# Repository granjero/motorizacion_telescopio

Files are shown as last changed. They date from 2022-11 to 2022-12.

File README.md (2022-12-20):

# 🔭 Montura Dobson Motorizada

https://github.com/granjero/telescopio

Proyecto para motorizar/robotizar la montura Dobson del telescopio modelo que se realiza en el curso de fabricación de telescopios de la ASARAMAS (https://amigosdelaastronomia.org/)  
&nbsp;  
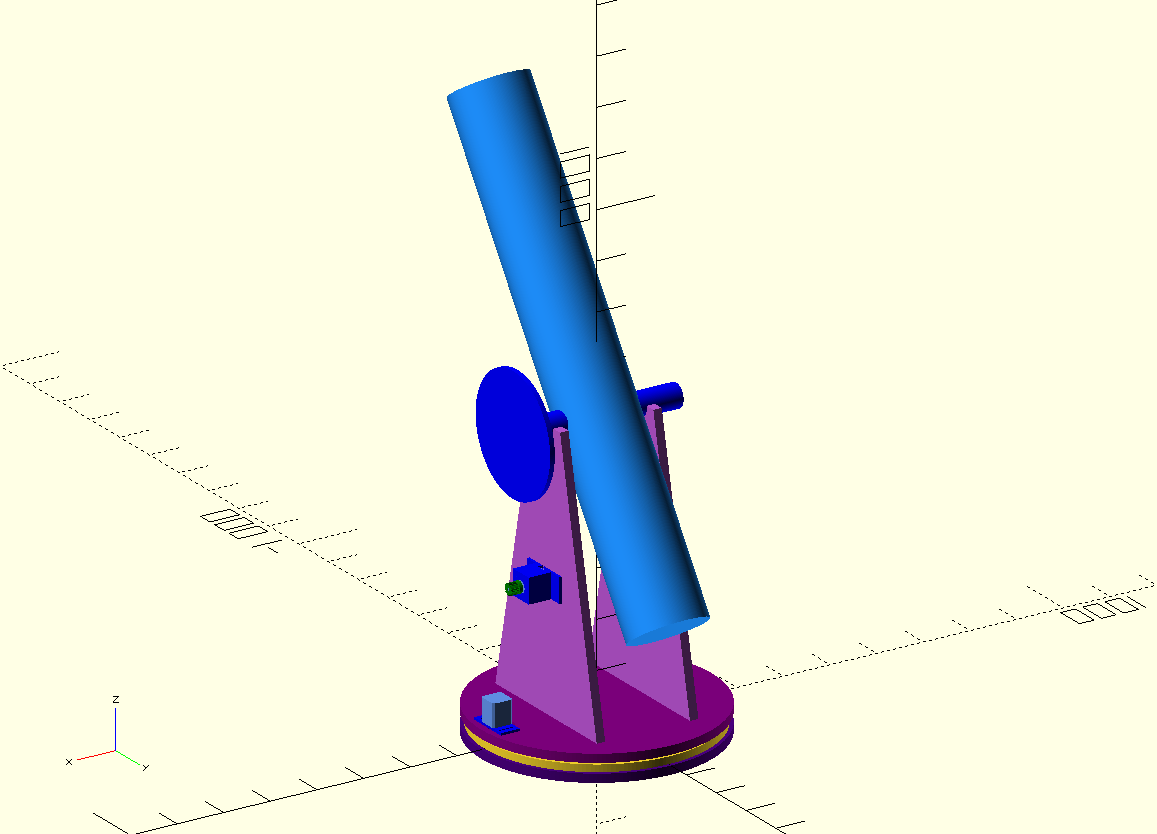
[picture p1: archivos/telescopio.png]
 &nbsp; &nbsp; &nbsp;

## 🚨 🚨 🚨 ¡¡¡ ADVERTENCIA !!! 🚨 🚨 🚨

El software de este proyecto **_NO_** impide que durante su recorrido el telescopio apunte al SOL ☀️  
Mirar el sol a través de un telescopio puede causar **CEGUERA IRREVERSIBLE** 👁 👨‍🦯 y/o daños a los esquipos.
Utilizar sólo cuando el sol se haya ocultado en el horizonte o con los filtros necesarios.

> Este software se proporciona "tal cual" y no se entrega ninguna garantía, expresa o implícita, en cuanto a su exactitud, integridad o rendimiento.  
> En ningún caso seré responsable de cualquier daño directo, indirecto, incidental, especial, consecuencial o ejemplar, resultante del uso del software de este proyecto.  
> El usuario asume el riesgo completo y la responsabilidad total en cuanto al uso y resultados del presente software.

### 📓 Resumen

En la [ASARAMAS](https://amigosdelaastronomia.org/) dictan un curso para fabricar un telescopio reflector del tipo Newtoniano con una montura tipo Dobson.  
El objetivo de este proyecto es automatizar la montura para que el telescopio localice y siga objetos celestes a demanda. Para ello se agregarán al telescopio dos motores. Uno para controlar el ángulo del Azimut y otro para controlar el ángulo de Elevación .  
Se interactúa con el telescopio a través de un panel de control que toma datos de [Stellarium](https://stellarium.org/) y los envia al microcontrolador del telescopio.  
La electrónica es muy sencilla, como microcontrolador se utiliza un ArduinoUNO, para manejar la potencia de los motores se pueden utilizar driver A4988 ó DRV8825 y un ShieldCNC para la conección.
En el proyecto están todos los archivos necesarios para imprimir o cortar las piezas y también están los scripts con los que fueron generadas.  
Seguir las instrucciones en orden.

### ⚙️ Instrucciones

- [Lista de Materiales](MATERIALES.md)
- [Hardware](/HARDWARE.md)
- [Firmware](/FIRMWARE.md)
- [Software](/SOFTWARE.md)

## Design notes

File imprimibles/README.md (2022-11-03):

# Telescopio Motorizado
Proyecto para motorizar la montura Dobson de mi telescopio casaero.
Más info en el futuro.

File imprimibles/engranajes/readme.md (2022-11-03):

# Engranajes

## Codigo para generar los engranajes necesarios.

### Instrucciones:

-   Descargar OpenScad -> https://openscad.org/
-   Abrir el archivo engranajes.scad
-   Modificar los parámetros según las medidas de la montura a motorizar
-   Comentar o descomentar las líneas necesarios.
-   Exportar las partes como archivos .stl para imprimir.

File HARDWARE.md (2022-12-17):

# HARDWARE

#### Instrucciones para ensamblar

## Azimut

El movimiento en el eje azimutal se realiza gracias a uno de los dos motores paso a paso.
El eje de este motor tiene asociado un _piñón_ de **X** dientes, que se acopla con una _corona_ de **Y** dientes.
Estos valores **X** e **Y**, junto con la cantidad de pasos del motor y la cantidad de microsteps configurados en el ShieldCNC son los que se deben volcar al firmware.

#### Corona

- 400 dientes

La corona se debe instalar centrada sobre la parte fija de la montura.  
&nbsp;  
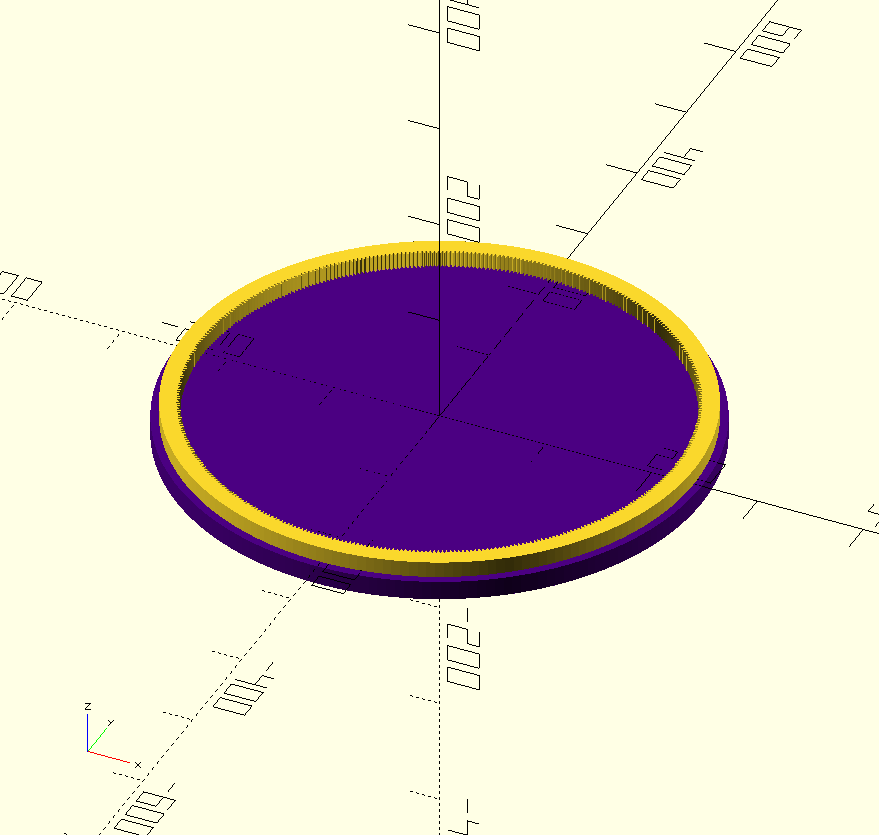
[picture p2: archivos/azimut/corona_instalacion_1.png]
 &nbsp; &nbsp; &nbsp;
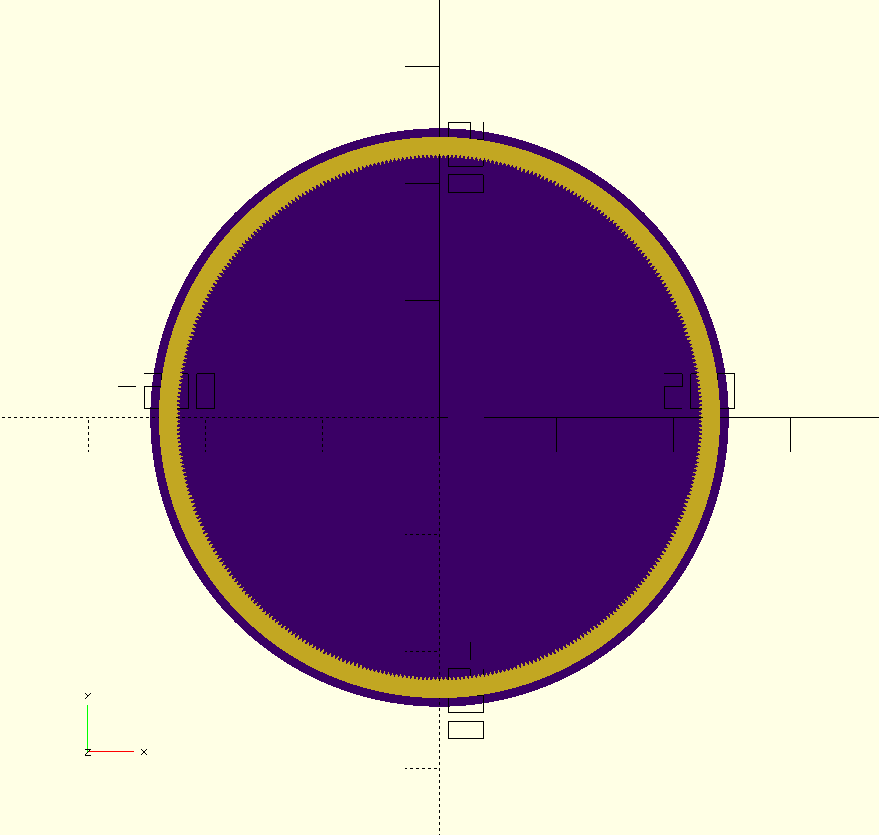
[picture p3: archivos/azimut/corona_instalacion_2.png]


Este es el [archivo](/imprimibles/engranajes/corona_400_dientes_azimut_LASER.dxf) para realizar el corte laser en MDF de 9mm de ancho, se puede generar una nueva pieza con otros parámetros usando este [sketch](/imprimibles/engranajes/engranajes.scad) de OpenScad.

#### Piñón

- 20 dientes

El piñon se debe instalar en el eje del motor con un tornillo y tuerca.  
&nbsp;  
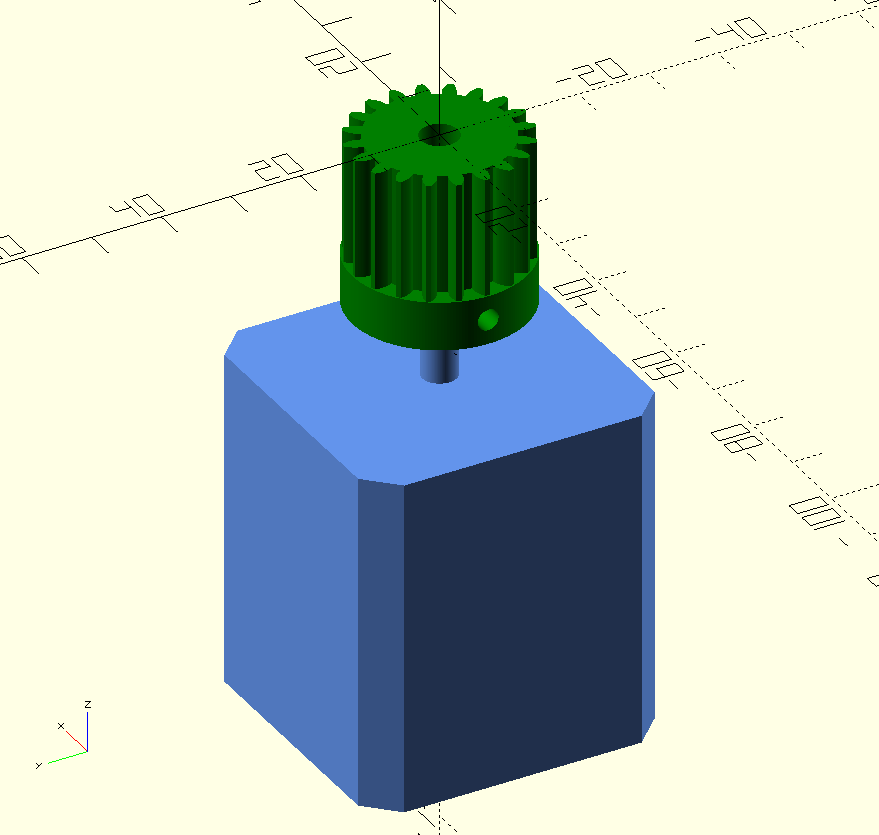
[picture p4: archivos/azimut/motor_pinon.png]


Este es el [archivo](/imprimibles/engranajes/pinon_20_dientes_azimut_3D.stl) para realizar la impresion 3D, se puede generar una nueva pieza con otros parámetros usando este [sketch](/imprimibles/engranajes/engranajes.scad) de OpenScad.

#### Soporte motor

El motor debe ser instalado con su eje paralelo al eje de rotación azimutal del telescopio y el piñón debe acoplar con la corona.
Para ello hay que realizar un orificio en la parte rotativa de la montura.  
&nbsp;  
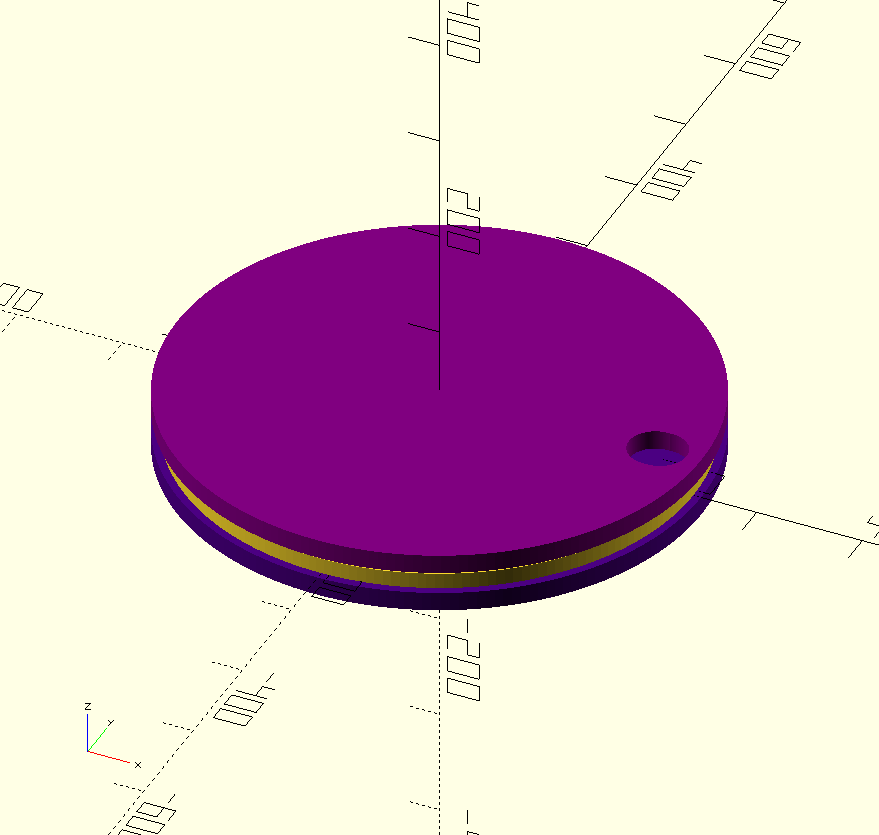
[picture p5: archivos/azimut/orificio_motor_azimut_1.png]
 &nbsp; &nbsp; &nbsp;
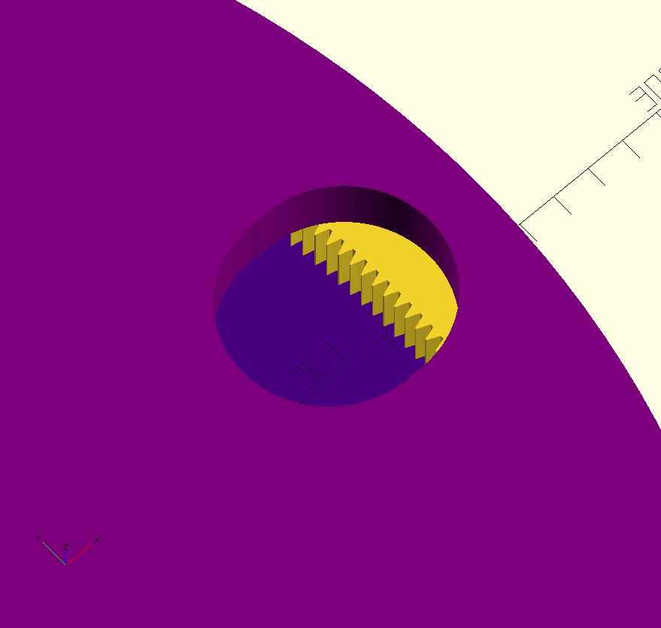
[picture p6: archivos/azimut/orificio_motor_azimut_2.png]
 &nbsp; &nbsp; &nbsp;
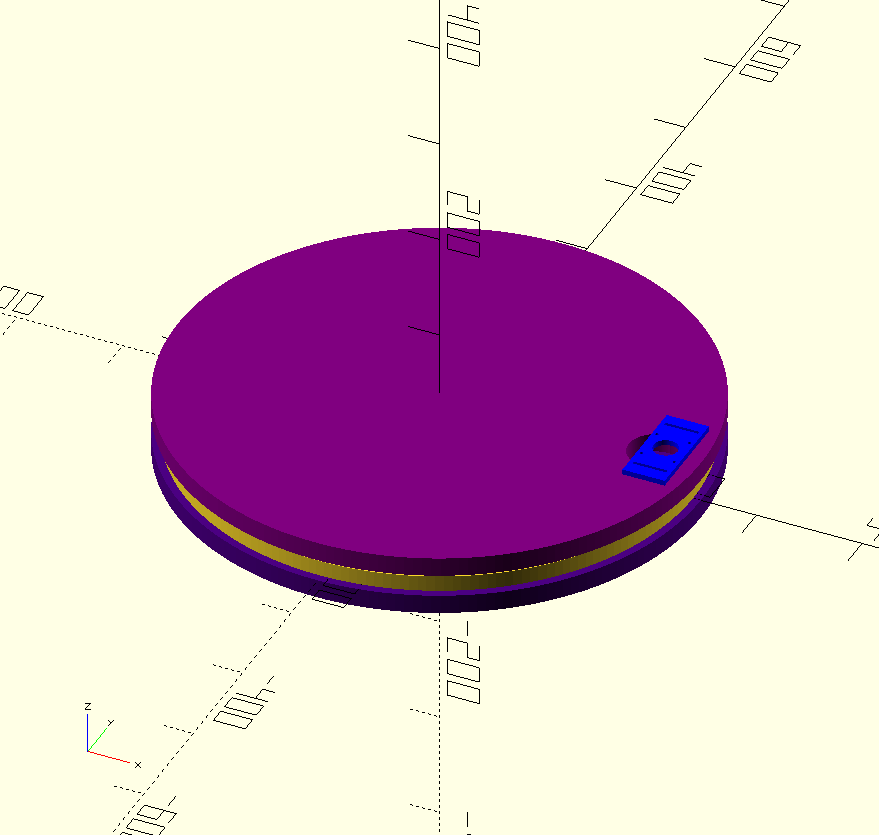
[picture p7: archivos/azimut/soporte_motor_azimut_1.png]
 &nbsp; &nbsp; &nbsp;
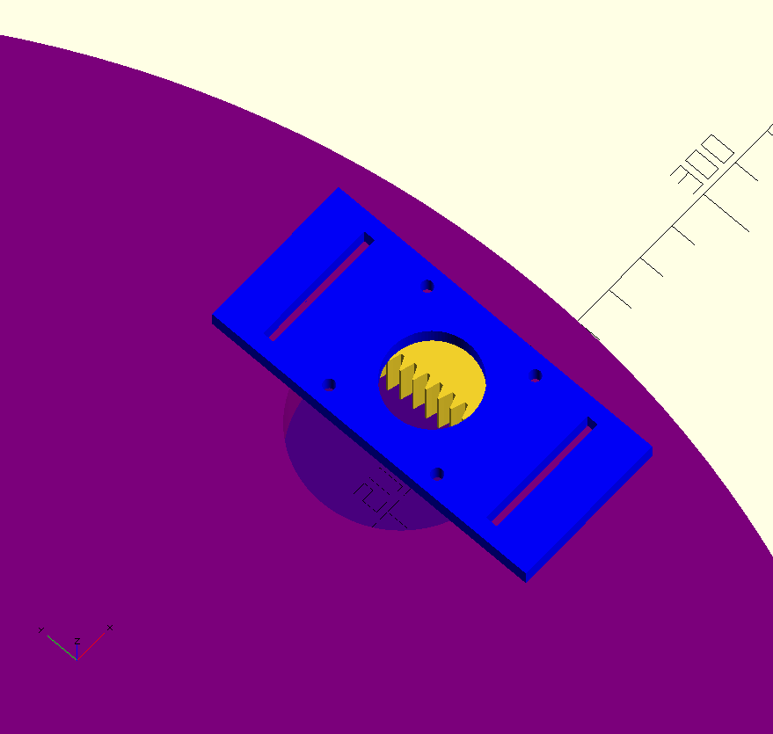
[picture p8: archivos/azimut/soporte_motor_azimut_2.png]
 &nbsp; &nbsp; &nbsp;
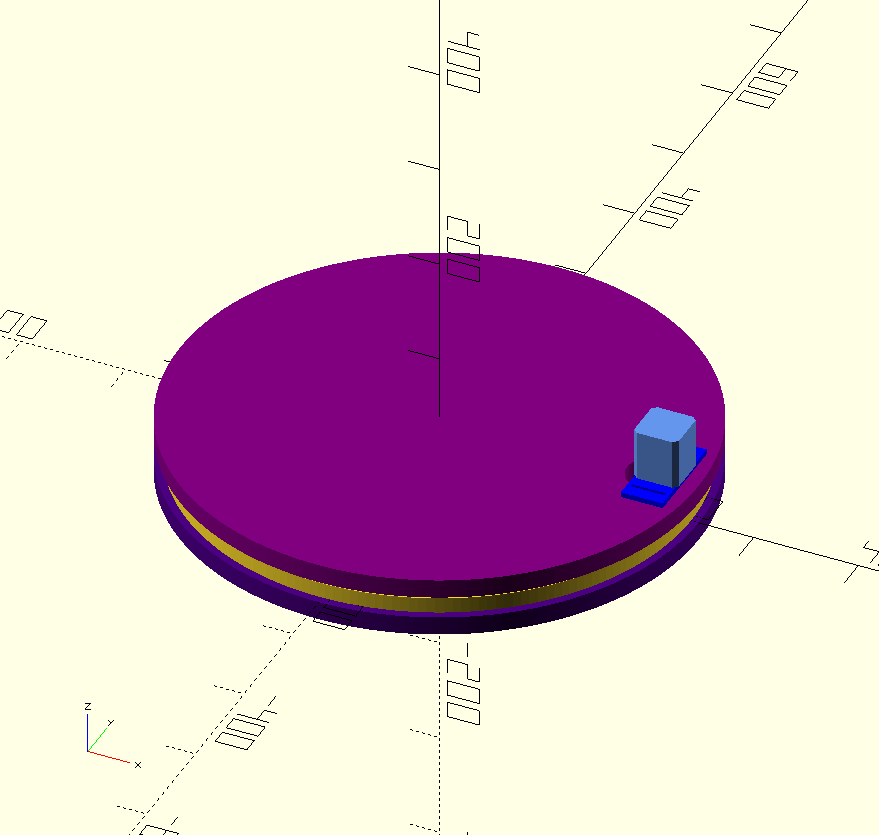
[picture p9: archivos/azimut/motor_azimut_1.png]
 &nbsp; &nbsp; &nbsp;
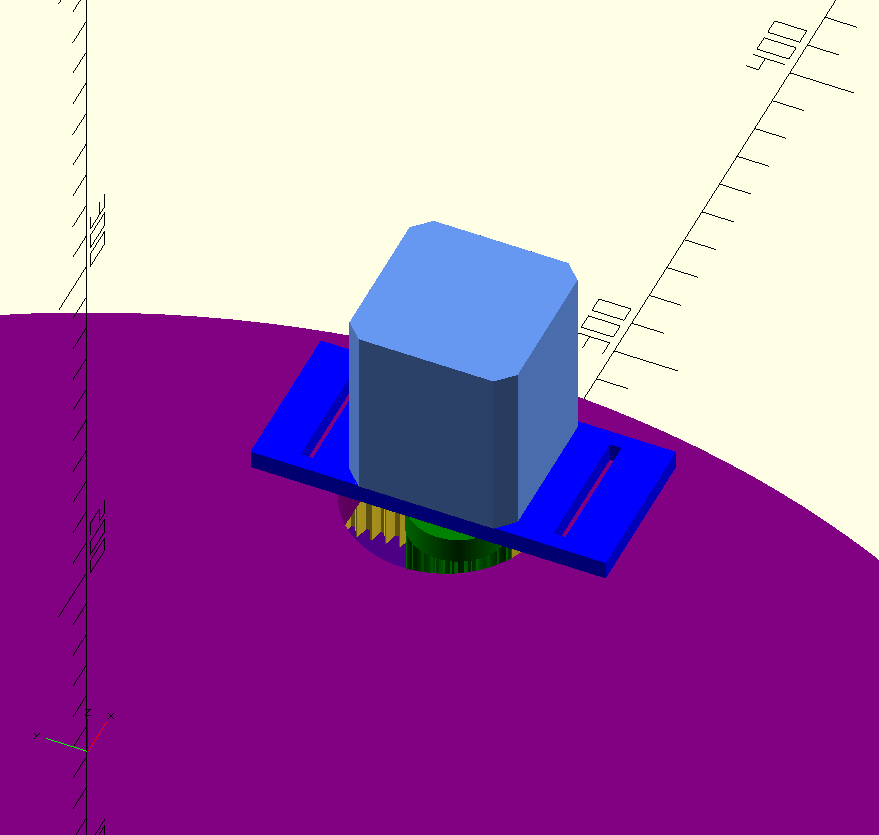
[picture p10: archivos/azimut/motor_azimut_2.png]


Con este [archivo](/imprimibles/monturas/montura_motor_azimut.stl) se puede realizar la impresion 3D del soporte.
También se puede cortar en metal con este [molde](/imprimibles/monturas/montura_motor_azimut_diy.pdf) _Al imprimir tener en cuenta que el PDF está en tamaño carta._

#### Motor

Conectar el motor al eje **X** del ShieldCNC.
Si gira en sentido contrario cuando se lo comanda con el panel del control invertir la conección.  
&nbsp;  
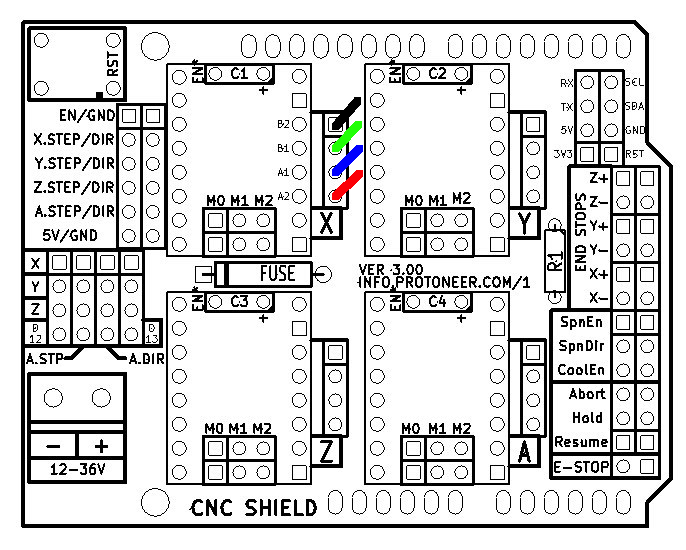
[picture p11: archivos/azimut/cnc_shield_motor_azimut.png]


## Elevación

El movimiento en el eje de la elevación se realiza gracias a uno de los dos motores paso a paso.
El eje de este motor tiene asociado un _piñón_ de **X** dientes, que se acopla a través de una correa dentada con una _corona_ de **Y** dientes.
Estos valores **X** e **Y**, junto con la cantidad de pasos del motor y la cantidad de microsteps configurados en el ShieldCNC son los que se deben volcar al firmware.

#### Corona

- 400 dientes

La corona se debe instalar centrada en el muñón del telescopio.  
&nbsp;  
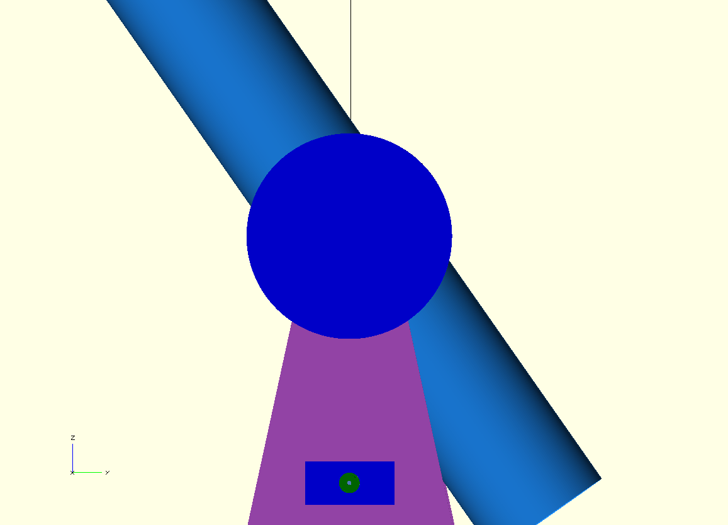
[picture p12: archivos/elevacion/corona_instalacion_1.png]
 &nbsp; &nbsp; &nbsp;
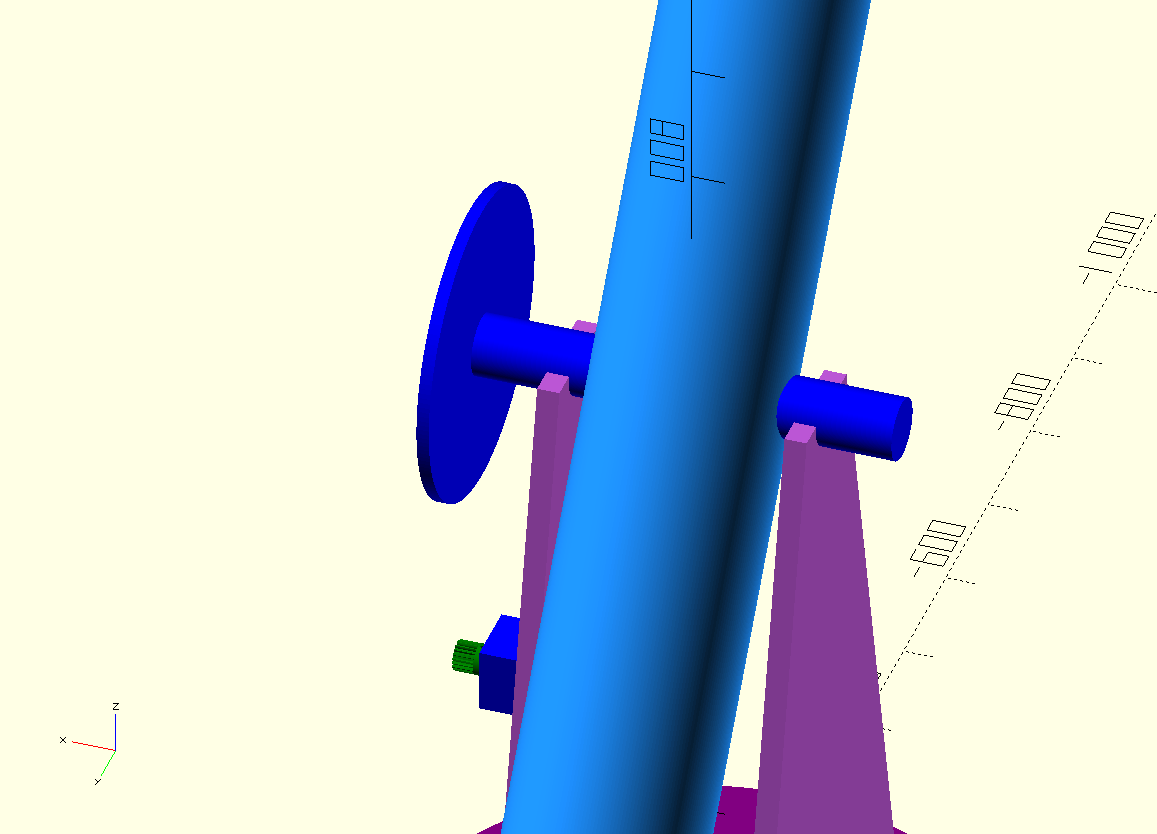
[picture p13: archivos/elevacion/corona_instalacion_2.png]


Este es el [archivo](/imprimibles/engranajes/corona_400_dientes_elevacion.dxf) para realizar el corte laser en MDF de 6mm de ancho, se puede generar una nueva pieza con otros parámetros usando este [sketch](/imprimibles/engranajes/engranajes.scad) de OpenScad.
Como guía para que la correa no se salga se coloca de cada lado de la corona un anillo un poco más grande que la corona. Este es el [archivo](/imprimibles/engranajes/anillos_corona_elevacion_LASER.dxf) para realizar el corte en MDF de 3mm

#### Piñón

- 20 dientes

El piñon se debe instalar en el eje del motor con sus tornillos.  
Polea GT2 de 20 dientes.  
&nbsp;  
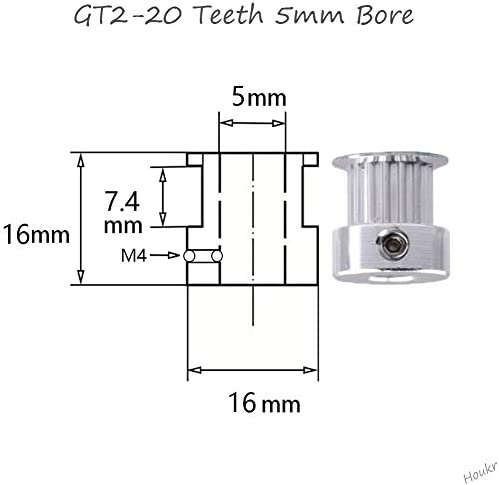
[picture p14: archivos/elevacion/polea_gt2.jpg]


#### Soporte motor

El motor debe ser instalado con su eje paralelo al eje de rotación de elevación del telescopio y el piñón debe acoplar con la corona con la correa.

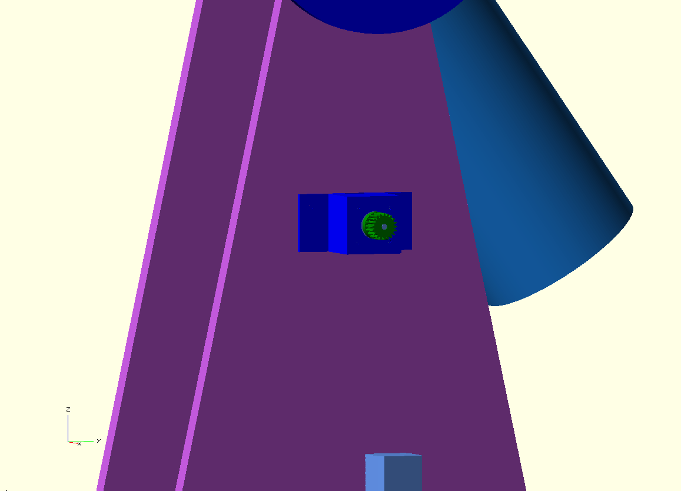
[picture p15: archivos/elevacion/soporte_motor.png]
 &nbsp; &nbsp; &nbsp;
&nbsp;  
Con este [archivo](/imprimibles/monturas/montura_motor_elevacion.stl) se puede realizar la impresion 3D del soporte.

#### Motor

Conectar el motor al eje **Y** del ShieldCNC.
Si gira en sentido contrario cuando se lo comanda con el panel del control invertir la conección.  
&nbsp;  
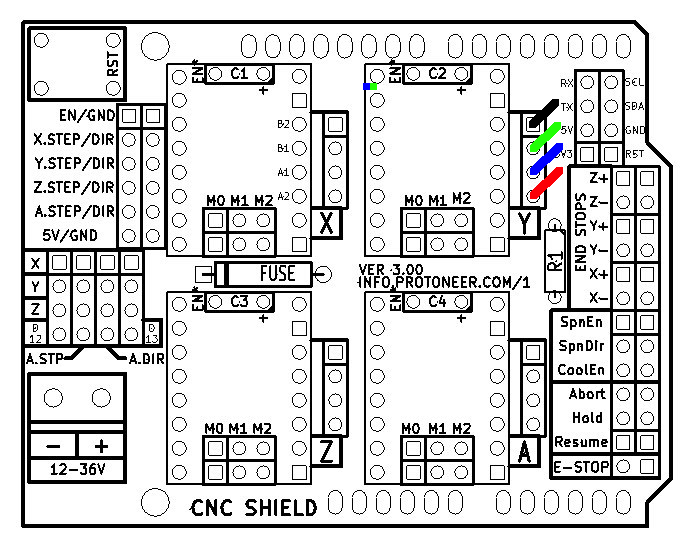
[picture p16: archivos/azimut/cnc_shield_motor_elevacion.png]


## Arduino + CNC Shield

1. Arduino
   1. Cargar el [firmware](/FIRMWARE.md) en el Arduino
   2. El Arduino será conectado a 12V por el puerto _PowerJack 2.1x5.5mm_  
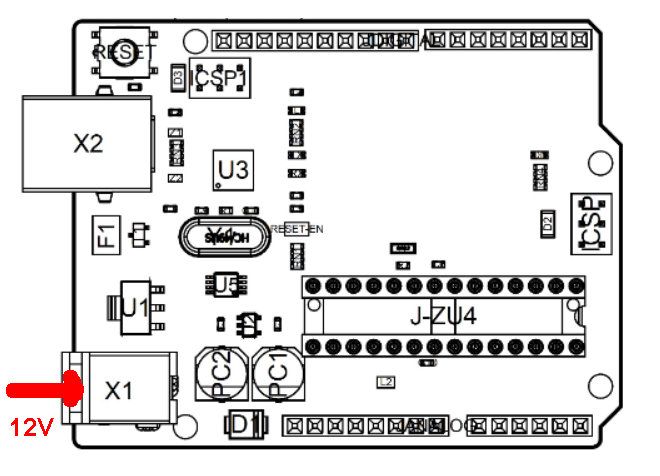
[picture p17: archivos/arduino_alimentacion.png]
      
2. ShieldCNC

   1. Popular con jumpers los 3 pares de pines (M0, M1, M2) del eje **X** y del eje **Y** para configurar el MicroStepping en 16.  
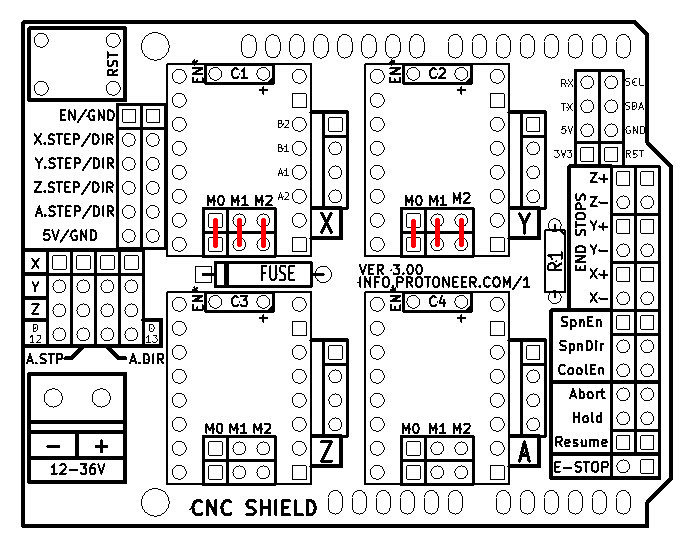
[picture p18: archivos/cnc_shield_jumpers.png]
      
   2. Conectar los drivers de los motores en el ShieldCNC en los headers para los ejes **X** e **Y**. El pin enable del driver debe coincidir con el pin enable del ShieldCNC  
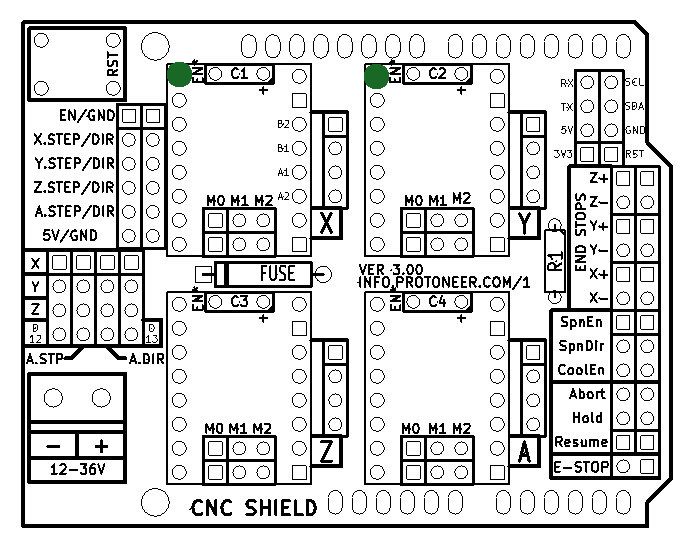
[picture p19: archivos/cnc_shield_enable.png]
      
   3. Conectar el cable de alimentacion al ShieldCNC  
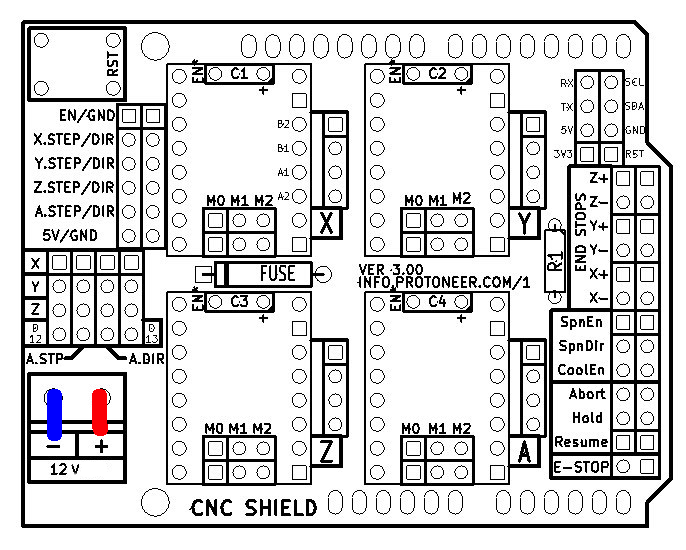
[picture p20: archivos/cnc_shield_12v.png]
      
   4. Conectar el ShieldCNC al Arduino

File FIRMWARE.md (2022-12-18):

# FIRMWARE

#### Instrucciones para cargar el firmware.

## Arduino IDE

1. [Descargar](https://github.com/arduino/arduino-ide/releases) el IDE de Arduino.
2. Ejecutar el IDE de Arduino
   - Conectar el Arduino al ordenador con el cable USB
   - Ir a Herramientas/Tools -> Placas/Boards y seleccionar Arduino UNO
   - Ir a Herramientas/Tools -> Puerto/Port y seleccionar el puerto en el que esté conectado el Arduino

## Firmware

Si se usaron las piezas estándar del proyecto saltear el paso 3 y pasar al paso 4.

3. Abrir el archivo telescopio.ino

Para que los movimientos del telescopio sean correctos el microcontrolador necesita conocer las relaciones entre los piñones y las coronas.  
Para que los cálculos sean correctos hay que modificar el Firmware y asignar a algunas constantes estos valores.

- Cambiar los valores de las constantes "PASOS_MOTOR\_", "MICROSTEPS\_", "DIENTES_CORONA\_", "DIENTES_PINON\_" para AZIMUT y ELEVACION según corresponda con la construccion del telescopio.
- Guardar el Sketch

4. Abrir el archivo telescopio.ino

   - Ir a Programa/Sketch -> Subir/Upload

5. Una vez subido el programa desconectar el Arduino del ordenador y continuar con la conección del Shield CNC. (Ver seccion Hardware)

##### Librerías utilizadas:

- [AccelStepper](https://www.airspayce.com/mikem/arduino/AccelStepper/)
- [SerialCommands](https://github.com/ppedro74/Arduino-SerialCommands)

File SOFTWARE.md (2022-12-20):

# SOFTWARE

#### Instrucciones de uso del Panel de Control .

El panel de control es un archivo html que se debe cargar en un navegador web que soporte comunicación serie como [Chromium](https://www.chromium.org/getting-involved/download-chromium/) o Chrome.
[Navegadores compatibles](https://developer.mozilla.org/en-US/docs/Web/API/SerialPort#browser_compatibility)  
A su vez este proyecto depende de Stellarium para obtener la ubicacion de los objetos celestes para enviarlos al telescopio.

## Stellarium

1. [Descargar](https://stellarium.org) stellarium 1.1 o superior.
2. Ejecutar Stellarium
3. Configuraciones

   1. Locación

      - Con F6 o a través del menú de la izquierda se ingresa al menú de Locación.
        &nbsp;  
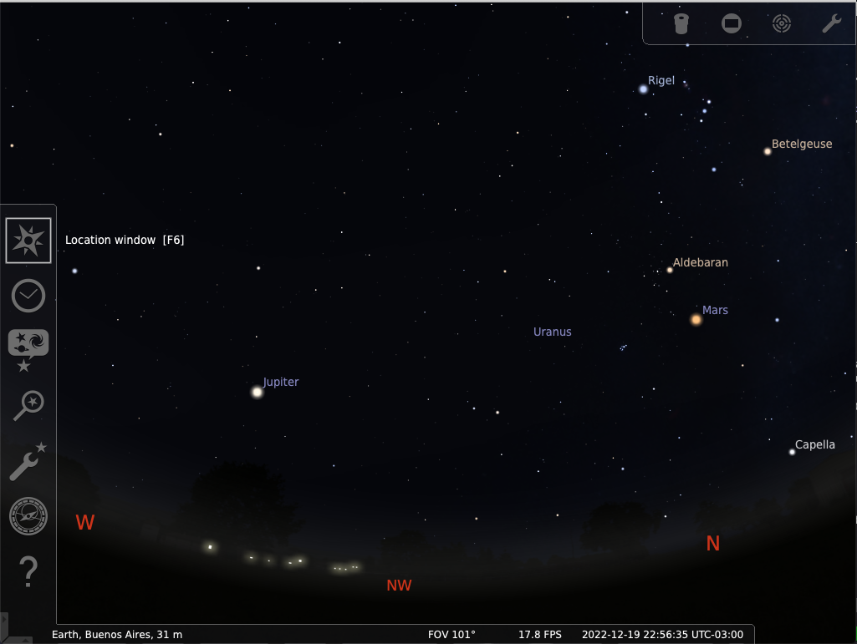
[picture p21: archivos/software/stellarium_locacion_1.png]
         &nbsp; &nbsp; &nbsp;
      - Setear latitud, longitud y altitud snm
        &nbsp;  
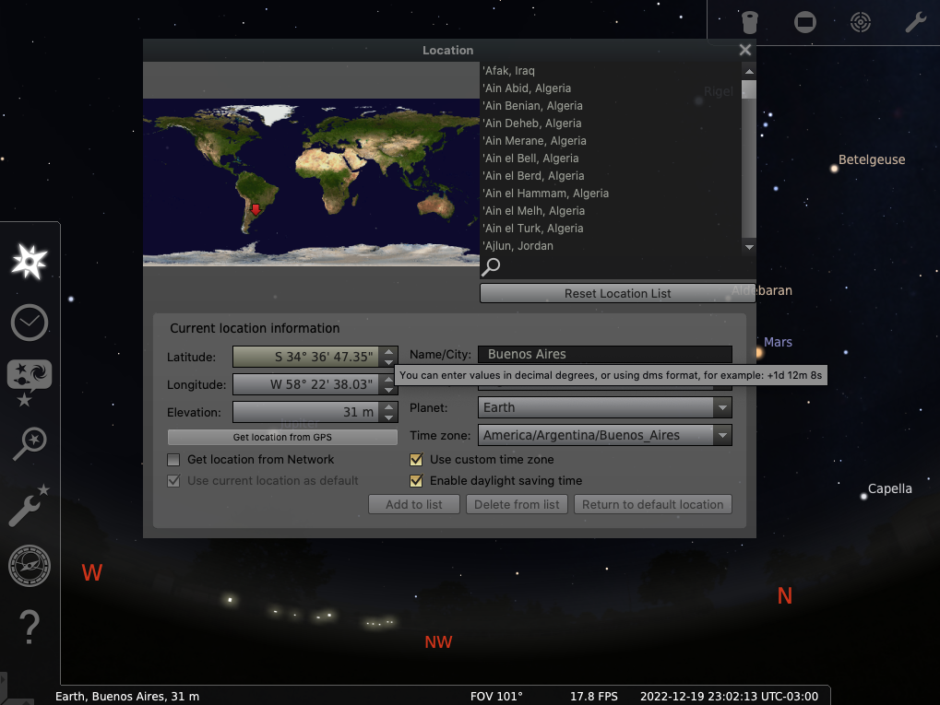
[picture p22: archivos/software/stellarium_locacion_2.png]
         &nbsp; &nbsp; &nbsp;

   2. Fecha y Hora

      - Con F5 o a través del menú de la izquierda se ingresa al menú de Fecha y Hora.
        &nbsp;  
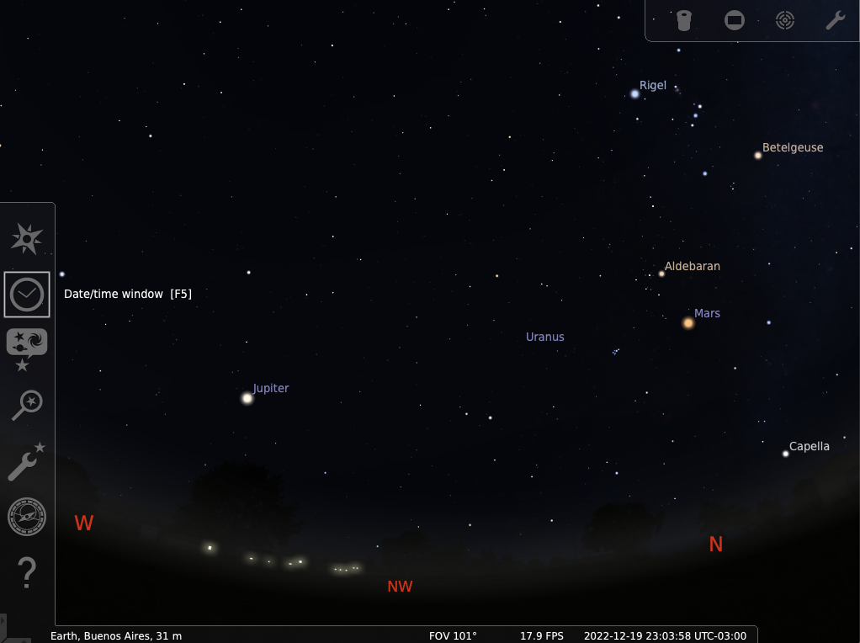
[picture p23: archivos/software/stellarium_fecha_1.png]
         &nbsp; &nbsp; &nbsp;
      - Setear correctamente la hora local.
        &nbsp;  
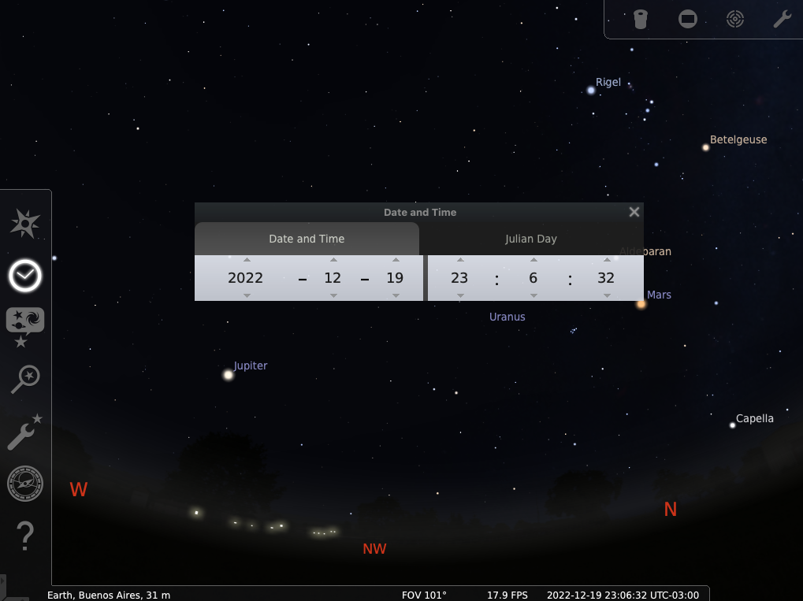
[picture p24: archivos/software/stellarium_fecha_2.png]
         &nbsp; &nbsp; &nbsp;

4. Plugin Control Remoto

   - Con F2 o a través del menú de la izquierda se ingresa al menú de configuraciones.
     &nbsp;  
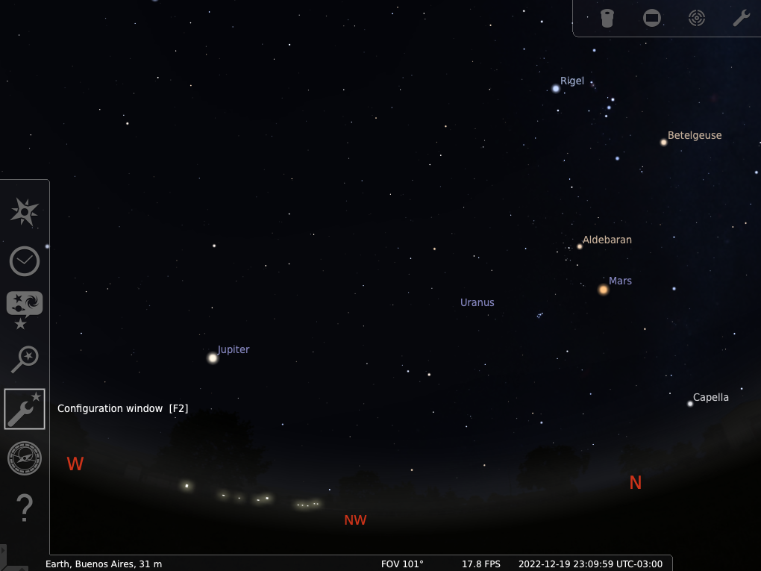
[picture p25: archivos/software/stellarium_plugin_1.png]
      &nbsp; &nbsp; &nbsp;
   - Ir a la solapa Plugins y seleccionar el Plugin _Remote Control_.
     &nbsp;  
      &nbsp; &nbsp; &nbsp;
   - Tildar la casilla _Load at Startup_ y reiniciar Stellarium para poder ingresar a la configuracion del mismo.
     Tildar la casilla Enable CORS for the following origin y en el campo poner un \*.
     _Leer advertencia al respecto del \* en stellarium_
     &nbsp;  
      &nbsp; &nbsp; &nbsp;

## Panel de Control

##### Librerías utilizadas:

- [Bootstrap](https://www.airspayce.com/mikem/arduino/AccelStepper/)
- [Font Awesome](https://github.com/ppedro74/Arduino-SerialCommands)

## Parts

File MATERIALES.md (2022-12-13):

## Materiales

- Telescopio
- Montura
- [Arduino UNO](https://docs.arduino.cc/static/9d6ed041fec691039663ae42f50fabcc/A000066-datasheet.pdf)
- [CNC Arduino Shield](https://blog.protoneer.co.nz/arduino-cnc-shield/)
- Driver [A4988](https://www.pololu.com/product/1182) x 2 ó [DRV8825](https://www.pololu.com/product/2133) x 2
- Fuente Switching tipo notebook 12V 3A
- [Motores Nema17](https://reprap.org/wiki/NEMA_17_Stepper_motor) x 2
- Soporte Motor Azimut
- Soporte Motor Elevación
- Piñón y Corona Azimut
- Piñón y Corona Elevación
- Correa cerrada GT2 Elevación

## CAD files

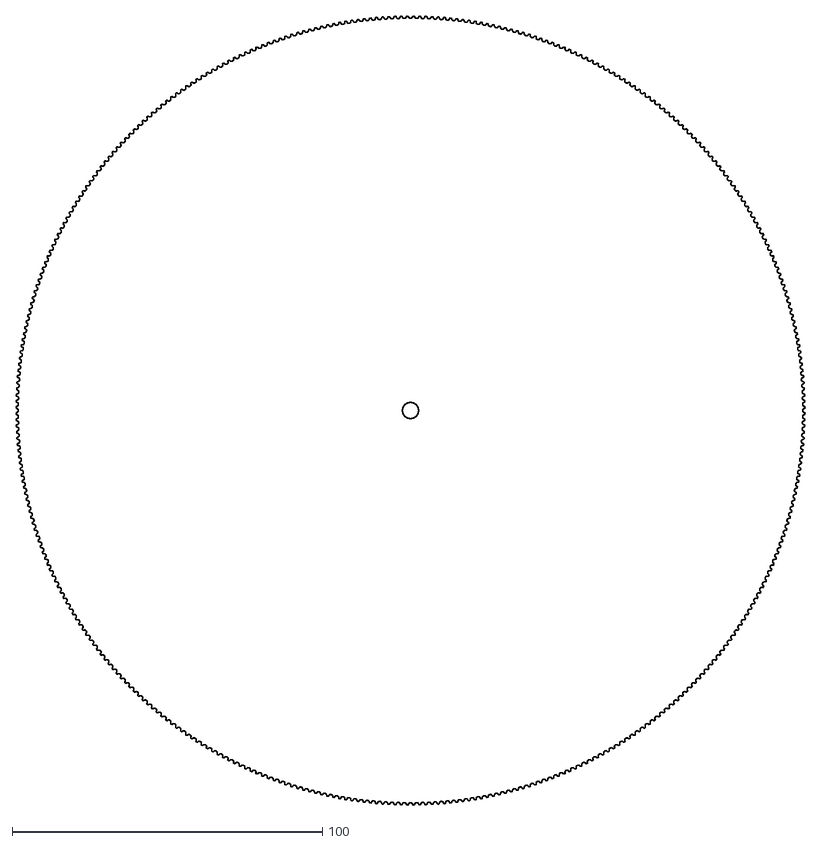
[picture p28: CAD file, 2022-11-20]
imprimibles/engranajes/corona_400_dientes_elevacion_LASER.dxf
254.1 x 254.1

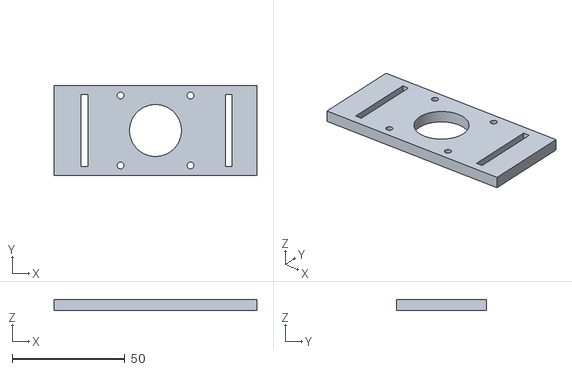
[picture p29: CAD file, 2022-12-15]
imprimibles/monturas/montura_motor_azimut.stl
90.0 x 40.0 x 5.00

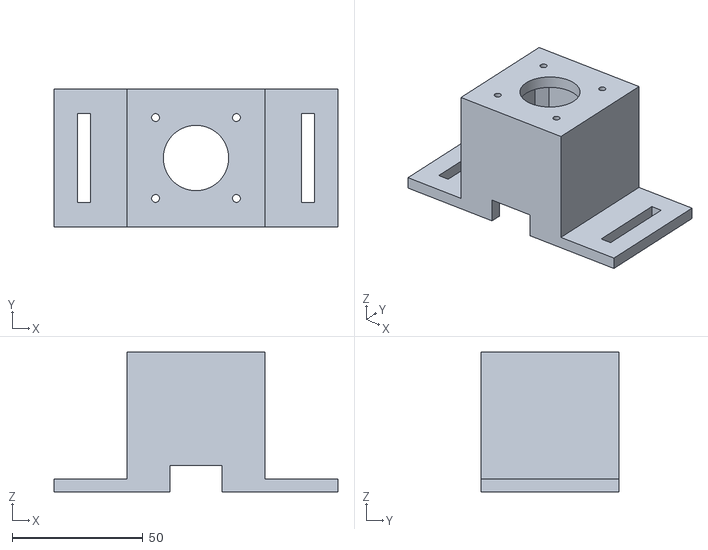
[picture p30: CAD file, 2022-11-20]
imprimibles/monturas/montura_motor_elevacion.stl
108.8 x 52.8 x 53.5

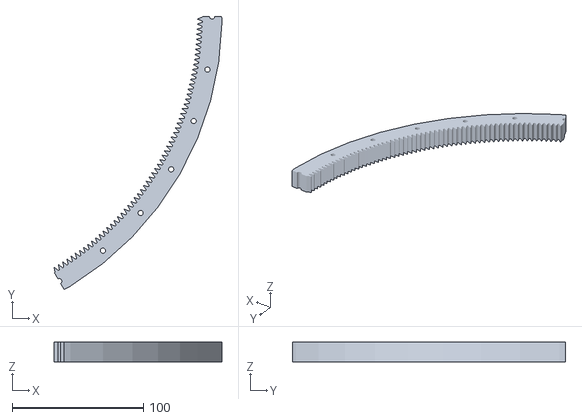
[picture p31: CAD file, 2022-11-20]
imprimibles/engranajes/corona_400_dientes_azimut_3D.stl
128.0 x 208.1 x 15.0

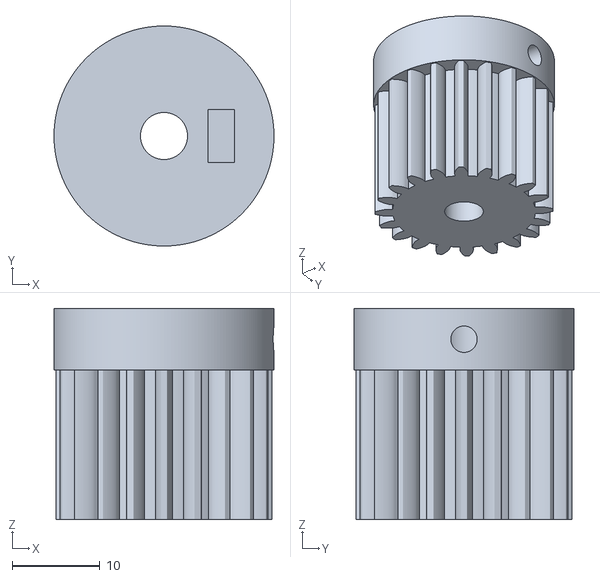
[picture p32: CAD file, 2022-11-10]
imprimibles/engranajes/pinon_20_dientes_azimut_3D.stl
25.0 x 25.0 x 24.0

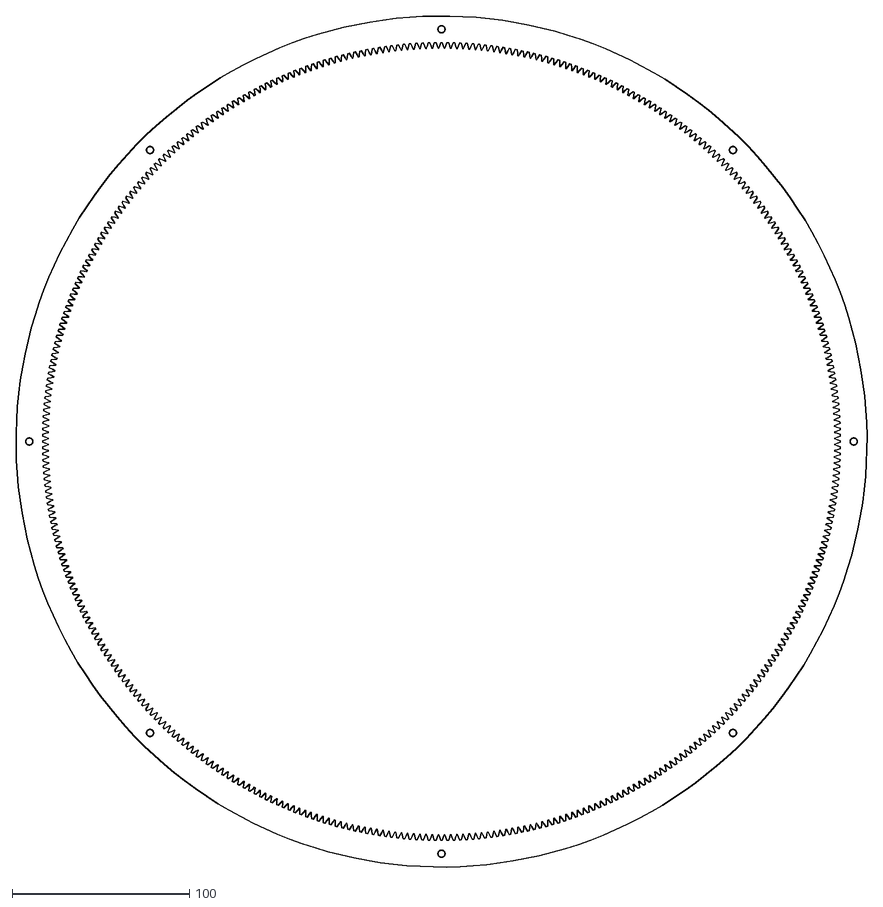
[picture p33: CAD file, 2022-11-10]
imprimibles/engranajes/corona_400_dientes_azimut_LASER.dxf
480.0 x 480.0

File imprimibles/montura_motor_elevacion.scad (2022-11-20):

$fn = 200;


alto_motor = 48;
ancho_motor = 42.6;
espesor_montura = 5;
    
soporte(ancho_motor, alto_motor, espesor_montura);

/*
difference()
{
    soporte(ancho_motor, alto_motor, espesor_montura);
    motor_cuerpo(alto_motor);
}

/*
difference()
{
    union(){
        
    translate([0,0,(alto_motor+espesor_montura)/2])
    cube(alto_motor+espesor_montura, center = true);
    translate([0,0,alto_motor+(espesor_montura/2)])
    cube([53, 93, 5], center = true);

    }

    translate([-20, 35, 20])
    cube([40, 5, 50]);
    translate([-20, -40, 20])
    cube([40, 5, 50]);
    motor_medio(alto_motor+espesor_montura);
    translate([0, -15, 40])
    cube([40, 30, 20]);

}
*/
    

/*

difference()
{
    union()
    {
        translate([0,0,53/2])
        cube(53, center = true);
        translate([0,0,50])
        cube([53, 93, 5], center = true);
    }
    
    motor_medio(53);

}
motor_top(5);
translate([0,0,50])
cube([53, 93, 5], center = true);
*/

/*
motor_top(5);
translate([0,0,5])
motor_medio(48);
*/

module soporte (ancho, alto, espesor)
{
    solapa = 33;
    esquina = 6;
    separacionTornillos = 31;

    difference()
    {
        difference()
        {
            translate([0,0,(alto+espesor)/2])
            cube([ancho + espesor * 2, ancho + espesor * 2, alto + espesor], center = true);
            motor_cuerpo(alto, ancho);
        }    

        // vastago
        translate([0, 0, (alto+espesor)/2])
        cylinder(h = alto + espesor, d = 25, center = true);
         
        // tornillos
        translate([separacionTornillos/2, separacionTornillos/2, (alto+espesor)/2])
        cylinder(h = alto + espesor, d = 3, center = true);
        translate([-separacionTornillos/2, separacionTornillos/2, (alto+espesor)/2])
        cylinder(h = alto + espesor, d = 3, center = true);
        translate([separacionTornillos/2, -separacionTornillos/2, (alto+espesor)/2])
        cylinder(h = alto + espesor, d = 3, center = true);
        translate([-separacionTornillos/2, -separacionTornillos/2, (alto+espesor)/2])
        cylinder(h = alto + espesor, d = 3, center = true);
        
        //enchufe
        translate([0,0, 5])
        cube([20, ancho * 2, 10], center = true);
    } 

    difference()
    {
        translate([ancho/2 + solapa/2, 0,espesor/2])    
        cube([solapa, ancho + espesor * 2, espesor], center = true);

        translate([ancho/2 + solapa/2 + espesor, 0,espesor/2])    
        cube([espesor, ancho * .8, espesor], center = true);
    }
    difference()
    {
        translate([-ancho/2 - solapa/2, 0,espesor/2])    
        cube([solapa, ancho + espesor * 2, espesor], center = true);

        translate([-ancho/2 - solapa/2 - espesor, 0,espesor/2])    
        cube([espesor, ancho * .8, espesor], center = true);

    }
    
    
        
}


module motor_top(alto, ancho)
{
    //alto = 5;
    //ancho = 42;
    esquina = 6;
    separacionTornillos = 31;
    
    translate([0,0, alto/2])
    difference()
    {
        cube([ancho, ancho, alto], center = true);
         
        // vastago
        cylinder(h = 5, d = 25, center = true);
         
        // tornillos
        translate([separacionTornillos/2, separacionTornillos/2, 0])
        cylinder(h = 10, d = 3, center = true);
        translate([-separacionTornillos/2, separacionTornillos/2, 0])
        cylinder(h = 10, d = 3, center = true);
        translate([separacionTornillos/2, -separacionTornillos/2, 0])
        cylinder(h = 10, d = 3, center = true);
        translate([-separacionTornillos/2, -separacionTornillos/2, 0])
        cylinder(h = 10, d = 3, center = true);
         
        // esquinas
        translate([ancho/2,ancho/2,0])
        rotate([0,0,45])
        cube([esquina, esquina, alto], center = true);

        translate([ancho/2,-ancho/2,0])
        rotate([0,0,45])
        cube([esquina, esquina, alto], center = true);

        translate([-ancho/2,ancho/2,0])
        rotate([0,0,45])
        cube([esquina, esquina, alto], center = true);

        translate([-ancho/2,-ancho/2,0])
        rotate([0,0,45])
        cube([esquina, esquina, alto], center = true);
    }
}

module motor_cuerpo(alto, ancho)
{
    
    //ancho = 42;
    esquina = 6;
//    alto = 4;
    separacionTornillos = 31;
    
    translate([0,0, alto/2])
    difference()
    {
        cube([ancho, ancho, alto], center = true);
         
        // esquinas
        translate([ancho/2,ancho/2,0])
        rotate([0,0,45])
        cube([esquina, esquina, alto], center = true);

        translate([ancho/2,-ancho/2,0])
        rotate([0,0,45])
        cube([esquina, esquina, alto], center = true);

        translate([-ancho/2,ancho/2,0])
        rotate([0,0,45])
        cube([esquina, esquina, alto], center = true);

        translate([-ancho/2,-ancho/2,0])
        rotate([0,0,45])
        cube([esquina, esquina, alto], center = true);
    }
}

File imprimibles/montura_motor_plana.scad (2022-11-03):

$fn = 100;

espesor = 3;
ancho = 40; 
largo = 60;
separacionTornillos = 31;


difference(){

//-------------
    difference(){
        cube([largo, ancho, espesor]);
        translate([largo * 0.5, ancho * 0.5, 0])
        cylinder(h = espesor*3, d = 23, center = true); 
    }
//-------------

//-------------
    translate(
        [(largo * 0.5) - (separacionTornillos * 0.5),
        (ancho * 0.5) - (separacionTornillos * 0.5),
        0])
    cylinder(h = 100, d = 3, center = true);
        
    translate(
        [(largo * 0.5) + (separacionTornillos * 0.5),
        (ancho * 0.5) - (separacionTornillos * 0.5),
        0])
    cylinder(h = 100, d = 3, center = true);

    translate(
        [(largo * 0.5) - (separacionTornillos * 0.5),
        (ancho * 0.5) + (separacionTornillos * 0.5),
        0])
    cylinder(h = 100, d = 3, center = true);

    translate(
        [(largo * 0.5) + (separacionTornillos * 0.5),
        (ancho * 0.5) + (separacionTornillos * 0.5),
        0])
    cylinder(h = 100, d = 3, center = true);
//-------------



    translate(
        [6, 
        (ancho * 0.5 - ancho * 0.4),
        0])
    cube([3, ancho * 0.8, 10]);

   



    translate(
        [largo -8, 
        (ancho * 0.5 - ancho * 0.4),
        0])
    cube([3, ancho * 0.8, 10]);
    
  
}

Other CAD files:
imprimibles/engranajes/anillos_corona_elevacion_LASER.dxf
imprimibles/monturas/montura_motor_azimut.scad
imprimibles/monturas/montura_motor_elevacion.scad
imprimibles/engranajes/engranajes.scad
imprimibles/engranajes/gears.scad

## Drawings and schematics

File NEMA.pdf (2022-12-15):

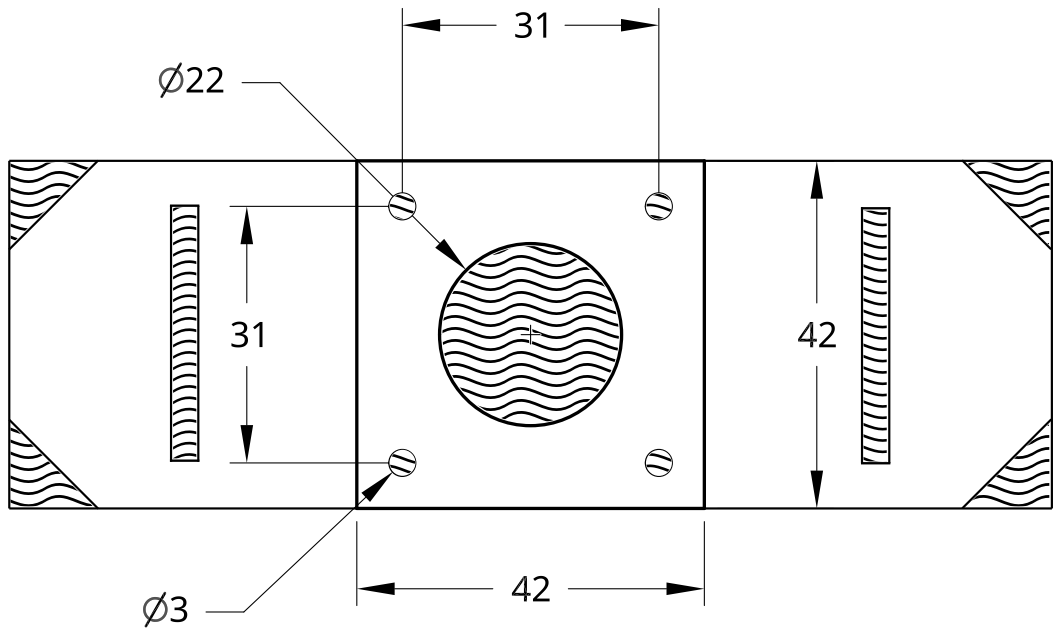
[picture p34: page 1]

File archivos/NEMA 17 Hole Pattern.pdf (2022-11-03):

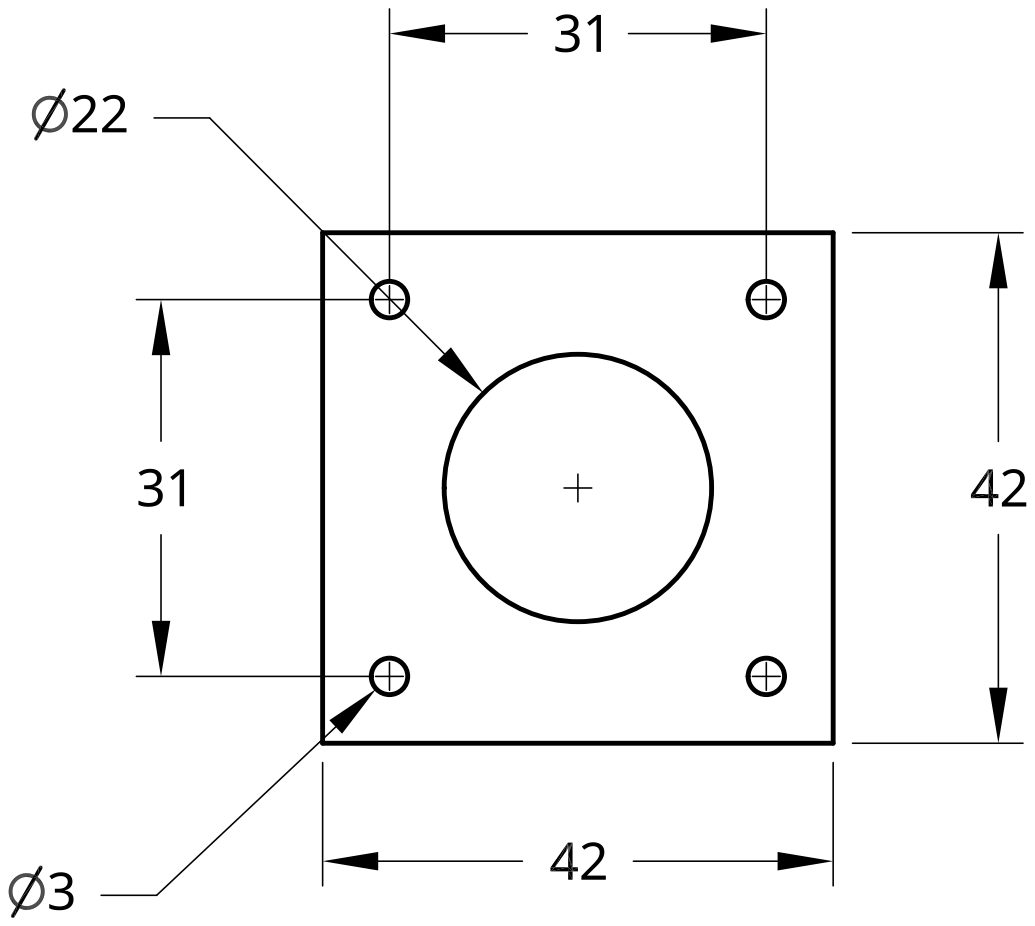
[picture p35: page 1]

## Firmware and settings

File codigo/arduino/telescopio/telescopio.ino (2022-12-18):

// librerias
#include <Arduino.h>
#include <math.h>
#include <AccelStepper.h>
#include <SerialCommands.h>

/* VALORES AZIMUT
 ***************/
#define PASOS_MOTOR_AZ 200L //  cant de pasos del motor (Dejar la L al final del numero)
#define MICROSTEPS_AZ 16 // microstepping = [full step = 1] [half step = 2] [quarter step = 4] [eighth step = 8] [sixteenth step = 16]
#define DIENTES_CORONA_AZ 400
#define DIENTES_PINON_AZ 20
/* VALORES ELEVACION 
 ******************/
#define PASOS_MOTOR_EL 200L //  cant de pasos del motor (Dejar la L al final del numero)
#define MICROSTEPS_EL 16 // microstepping = [full step = 1] [half step = 2] [quarter step = 4] [eighth step = 8] [sixteenth step = 16]
#define DIENTES_CORONA_EL 400
#define DIENTES_PINON_EL 20
/* VALORES COMUNES 
 ****************/
#define VEL_MAX 1000
#define ACELERACION 500

/* NO DEBERIA HACER FALTA MODIFICAR NADA DEBAJO DE ESTA LINEA 
 ************************************************************/

// constantes
#define ENABLE_PIN 8 // pin del Arduino conectado al enable de los drivers de los motores


// variables
bool andando = true;
bool constante = false;

// inicializacion de los motores
AccelStepper azimut(AccelStepper::DRIVER, 2, 5);
AccelStepper elevacion(AccelStepper::DRIVER, 3, 6);

// SerialCommands
char serial_command_buffer_[32];
SerialCommands serial_commands_(&Serial, serial_command_buffer_, sizeof(serial_command_buffer_), "\r\n", " ");

// funciones serial
// ****************
//This is the default handler, and gets called when no other command matches. 
void cmd_unrecognized(SerialCommands* sender, const char* cmd)
{
    sender->GetSerial()->print("Unrecognized command [");
    sender->GetSerial()->print(cmd);
    sender->GetSerial()->println("]");
}

// SEGUIMIENTO
// comando serial: SEG azimut elevacion
void cmd_seguimiento(SerialCommands* sender)
{
    char* AZ = sender->Next();
    char* EL = sender->Next();

    andando = true;
    constante = false;

    azimut.enableOutputs(); 
    azimut.setMaxSpeed(VEL_MAX);
    azimut.moveTo(anguloAzimutAPaso(atof(AZ)));

    elevacion.enableOutputs(); 
    elevacion.setMaxSpeed(VEL_MAX);
    elevacion.moveTo(anguloElevacionAPaso(atof(EL)));

    /*sender->GetSerial()->print("AZ: ");*/
    /*sender->GetSerial()->println(AZ);*/
    /*sender->GetSerial()->print("EL: ");*/
    /*sender->GetSerial()->println(EL);*/
}

/*MOTOR AZIMUT*/
/*------------*/
// MOTOR AZIMUT VELOCIDAD CONSTANTE
// comando serial: AZ velocidad
void cmd_azimut_vel_cte(SerialCommands* sender)
{
    char* velocidad = sender->Next();
    // TODO controlar que atol(velocidad) esté entre 0 y VEL_MAX
    andando = true;
    constante = true;

    azimut.enableOutputs(); 
    azimut.setMaxSpeed(VEL_MAX);
    azimut.setSpeed(atol(velocidad));
    sender->GetSerial()->print("Velocidad motor AZIMUT: ");
    sender->GetSerial()->println(velocidad);
}
// MOTOR AZIMUT IR A POSICION SEGUN ANGULO
// comando serial: AZp angulo velocidad
void cmd_azimut_pos(SerialCommands* sender)
{
    char* angulo = sender->Next();
    char* velocidad = sender->Next();
    // TODO controlar que atol(velocidad) esté entre 0 y VEL_MAX
    // TODO controlar que anguloAzimutAPaso se encuentre entre 0 y 360
    andando = true;
    constante = false;

    azimut.enableOutputs(); 
    azimut.setMaxSpeed(atoi(velocidad));
    azimut.moveTo(anguloAzimutAPaso(atof(angulo)));
    sender->GetSerial()->print("Angulo destino motor AZIMUT: ");
    sender->GetSerial()->println(angulo);
    sender->GetSerial()->print("Velocidad motor AZIMUT: ");
    sender->GetSerial()->println(velocidad);
}
// MOTOR AZIMUT AVANZA X
// comando serial: AZa grados velocidad
void cmd_azimut_avanza(SerialCommands* sender)
{
    char* grados = sender->Next();

    andando = true;
    constante = false;

    azimut.enableOutputs(); 
    azimut.setMaxSpeed(VEL_MAX);
    azimut.moveTo(
            azimut.currentPosition() + anguloAzimutAPaso(atof(grados))
            );
    sender->GetSerial()->print("Mueve:  ");
    sender->GetSerial()->println(grados);
}
/*MOTOR ELEVACION*/
/*---------------*/
// MOTOR ELEVACION VELOCIDAD CONSTANTE
// comando serial: EL velocidad
void cmd_elevacion_vel_cte(SerialCommands* sender)
{
    char* velocidad = sender->Next();
    
    andando = true;
    constante = true;

    elevacion.enableOutputs(); 
    elevacion.setMaxSpeed(VEL_MAX);
    elevacion.setSpeed(atoi(velocidad));
    sender->GetSerial()->print("EL vel: ");
    sender->GetSerial()->println(velocidad);
}
// MOTOR ELEVACION IR A POSICION SEGUN ANGULO
// comando serial: ELp angulo velocidad
void cmd_elevacion_pos(SerialCommands* sender)
{
    char* angulo = sender->Next();
    char* velocidad = sender->Next();

    andando = true;
    constante = false;

    elevacion.enableOutputs(); 
    elevacion.setMaxSpeed(atoi(velocidad));
    elevacion.moveTo(anguloElevacionAPaso(atof(angulo)));
    sender->GetSerial()->print("ELEVACION angulo: ");
    sender->GetSerial()->println(angulo);
    sender->GetSerial()->print(" Posicion: ");
    sender->GetSerial()->print(anguloElevacionAPaso(atof(angulo)));
    sender->GetSerial()->print(" Vel: ");
    sender->GetSerial()->println(velocidad);
}
// MOTOR ELEVACION AVANZA X
// comando serial: ELa grados velocidad
void cmd_elevacion_avanza(SerialCommands* sender)
{
    char* grados = sender->Next();

    andando = true;
    constante = false;

    elevacion.enableOutputs(); 
    elevacion.setMaxSpeed(VEL_MAX);
    elevacion.moveTo(
            elevacion.currentPosition() + anguloElevacionAPaso(atof(grados))
            );
    sender->GetSerial()->print("Mueve:  ");
    sender->GetSerial()->println(grados);

}

// SET HOME 
void cmd_set_home(SerialCommands* sender)
{
    andando = false;
    constante = false;

    azimut.stop();
    elevacion.stop();
    azimut.disableOutputs(); // uso azimut pero podría usar elevacion porque compraten el pin
    azimut.setCurrentPosition(0);
    elevacion.setCurrentPosition(anguloElevacionAPaso(90));
    azimut.enableOutputs(); // uso azimut pero podría usar elevacion porque compraten el pin

    sender->GetSerial()->print("ELEVACION 90 AZIMUT 360");
}

// SET NEW HOME 
void cmd_set_new_home(SerialCommands* sender)
{
    andando = true;
    constante = false;

    char* az = sender->Next();
    char* el = sender->Next();

    long azPosActual = azimut.currentPosition();
    long azPosASumar = anguloAzimutAPaso(atof(az));

    long elPosActual = elevacion.currentPosition();
    long elPosASumar = anguloElevacionAPaso(atof(el));

    azimut.setCurrentPosition(azPosActual + azPosASumar);
    elevacion.setCurrentPosition(elPosActual + elPosASumar);
    /*azimut.setCurrentPosition(azimut.currentPosition() + anguloAzimutAPaso(atof(az)));*/
    /*elevacion.setCurrentPosition(elevacion.currentPosition() + anguloElevacionAPaso(atof(el)));*/
}

// GO HOME (u r drunk)
void cmd_go_home(SerialCommands* sender)
{
    andando = true;
    constante = false;

    elevacion.enableOutputs(); 
    elevacion.setMaxSpeed(VEL_MAX);
    elevacion.moveTo(anguloElevacionAPaso(90));
    azimut.enableOutputs();
    azimut.setMaxSpeed(VEL_MAX);
    azimut.moveTo(anguloElevacionAPaso(0));

    sender->GetSerial()->print("Yendo a Casa ");

}
// OFF apaga los motores
void cmd_off(SerialCommands* sender)
{
    andando = true; // para que deje de contar pasos.
    constante = false;

    /*azimut.stop();*/
    /*elevacion.stop();*/
    azimut.disableOutputs(); // uso azimut pero podría usar elevacion porque compraten el pin
    sender->GetSerial()->println("MOTORES OFF");
}

// STOP detiene los motores
void cmd_stop(SerialCommands* sender)
{
    andando = true; // para que deje de contar pasos.
    constante = false;

    azimut.stop();
    elevacion.stop();
    /*azimut.disableOutputs(); // uso azimut pero podría usar elevacion porque compraten el pin*/
    sender->GetSerial()->println("MOTORES STOP");
}
// funciones serial command
// ************************
// declaracion de variables a enviar por serial
SerialCommand cmd_seguimiento_("SEG", cmd_seguimiento);
SerialCommand cmd_azimut_vel_cte_("AZ", cmd_azimut_vel_cte);
SerialCommand cmd_azimut_pos_("AZp", cmd_azimut_pos);
SerialCommand cmd_azimut_avanza_("AZa", cmd_azimut_avanza);
SerialCommand cmd_elevacion_vel_cte_("EL", cmd_elevacion_vel_cte);
SerialCommand cmd_elevacion_pos_("ELp", cmd_elevacion_pos);
SerialCommand cmd_elevacion_avanza_("ELa", cmd_elevacion_avanza);
SerialCommand cmd_go_home_("GO_HOME", cmd_go_home);
SerialCommand cmd_set_home_("SET_HOME", cmd_set_home);
SerialCommand cmd_set_new_home_("NEW_HOME", cmd_set_new_home);
SerialCommand cmd_off_("OFF", cmd_off);
SerialCommand cmd_stop_("STOP", cmd_stop);

// angulo a nro de paso
// @param angulo de destino
// @return numero de paso correspondiente al angulo
long anguloElevacionAPaso(float angulo)
{
    return round((angulo * PASOS_MOTOR_EL * MICROSTEPS_EL * (DIENTES_CORONA_EL / DIENTES_PINON_EL)) / 360);
}
// @param angulo de destino
// @return numero de paso correspondiente al angulo
long anguloAzimutAPaso(float angulo)
{

    long pasosUnaVueltaMotor = PASOS_MOTOR_AZ * MICROSTEPS_AZ;
    long relacionEngranajes = DIENTES_CORONA_AZ / DIENTES_PINON_AZ;
    long pasosUnaVuelta360 = pasosUnaVueltaMotor * relacionEngranajes;
    long pasosUnGrado = pasosUnaVuelta360 / 360;
    long pasosAngulo = round(angulo * pasosUnGrado);

    return pasosAngulo;
}

// ************
// ************

void setup() {
    Serial.begin(115200); // comienza la comunicacion serial

    // inicializacion de los comandos definidos
    serial_commands_.SetDefaultHandler(&cmd_unrecognized);
    serial_commands_.AddCommand(&cmd_seguimiento_);
    serial_commands_.AddCommand(&cmd_azimut_vel_cte_);
    serial_commands_.AddCommand(&cmd_azimut_pos_);
    serial_commands_.AddCommand(&cmd_azimut_avanza_);
    serial_commands_.AddCommand(&cmd_elevacion_vel_cte_);
    serial_commands_.AddCommand(&cmd_elevacion_pos_);
    serial_commands_.AddCommand(&cmd_elevacion_avanza_);
    serial_commands_.AddCommand(&cmd_go_home_);
    serial_commands_.AddCommand(&cmd_set_home_);
    serial_commands_.AddCommand(&cmd_set_new_home_);
    serial_commands_.AddCommand(&cmd_off_);
    serial_commands_.AddCommand(&cmd_stop_);

    Serial.println("Motores Telescopio 0.1 -> Ready");

    // motor AZIMUT
    azimut.setPinsInverted(false, false, true); // el pin enable funciona cuando está el LOW.
    azimut.setEnablePin(ENABLE_PIN);
    azimut.setMaxSpeed(VEL_MAX);
    azimut.setAcceleration(ACELERACION);
    azimut.setSpeed(0);

    // motor ELEVACION
    elevacion.setPinsInverted(false, false, true); // el pin enable funciona cuando está el LOW.
    elevacion.setEnablePin(ENABLE_PIN);
    elevacion.setMaxSpeed(VEL_MAX);
    elevacion.setAcceleration(ACELERACION);
    elevacion.setSpeed(0);

    azimut.disableOutputs(); // uso azimut pero podría usar elevacion porque compraten el pin
}

void loop() {

	serial_commands_.ReadSerial(); // SerialCommands

    if(andando)
    {
        if(constante)
        {
            azimut.runSpeed();
            elevacion.runSpeed();
        }
        else
        {
            azimut.run();
            elevacion.run();
        }
    }
    /*Serial.println(azimut.currentPosition());*/
}

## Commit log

2022-11-03 ordenamiento del proyecto unifico 3d y archivos misc
    [engranajes.scad, gears.scad, montura_motor_plana.scad]
2022-11-03 muevo codigo arduino dentro de su carpeta
2022-11-04 enable pin magics
2022-11-04 movimientos motores
2022-11-06 juli hizo lo de serial
    [engranajes.scad]
2022-11-06 diagramas arduino cnc shield
2022-11-06 mejoras funciones de movimiento
    [engranajes.scad]
2022-11-06 cambios en el diseño del piñon
    [engranajes.scad, pinon_mejorado.stl]
2022-11-07 font awesome para la GUI
2022-11-07 orden codigo, funciones de avanzar y home
2022-11-08 tratando de obtener datos del servidor local de stellarium
2022-11-10 cambio microstepping y cosas de js que no andan
2022-11-10 piñon 3d
    [corona_400_dientes.dxf, engranajes.scad, pinon_20_dientes.stl]
2022-11-12 trabajando en el panel, bootstrap, fontawesome
2022-11-14 trabajando en el panel
2022-11-15 trabajando en el panel funciones js
2022-11-20 soporte motor elevacion
    [montura_motor_elevacion.scad, montura_motor_elevacion.stl]
2022-11-20 orden de archivos 3d y laser
    [anillos_corona_elevacion_LASER.dxf, corona_400_dientes_azimut_3D.stl, corona_400_dientes_azimut_LASER.dxf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]
2022-11-21 engranajes menu - telescopio.ino serial
    [engranajes.scad]
2022-11-22 anda el serial
2022-12-01 cambio calculo de angulo a pasos
2022-12-12 pasé unos atol to atof en los llamas a la funcion anguloAPaso
2022-12-12 borre la carpeta build que no hace al proyecto
2022-12-12 readme materiales
2022-12-18 arreglo en set new home
    [telescopio.ino]
2023-03-09 panel cambios para pantallas chicas
